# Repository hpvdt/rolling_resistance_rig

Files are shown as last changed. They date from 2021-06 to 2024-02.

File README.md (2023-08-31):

# Rolling Resistance Rig (RRR)

One of the most crucial aspects of our land vehicles is the study of rolling resistance and our pursuit of reducing it. To this end the team has constucted a rolling resistance rig (_RRR_) to characterize different wheels. This repository serves as **the definitive** collection of information related to the RRR and its tests: especially the sensor system design and data processing. 

The general principle of the RRR is that there is a large drum which acts as the riding surface for the wheel and is spun up to speed by an electric motor to simulate speeds of over 80 km/h. The wheel under test is installed above the wheel and is loaded to a similar level to the expected vehicle load prior to the drum getting spun up. Once the desired speed is achieved by the system, the power to the drum is cut and the drum/wheel combo is left to slow down by dissipating power primarily through their own rolling resistances.

During this slowdown the rotational period of each part is monitored and recorded over serial to then be analyzed and derive a rolling resistance for the wheel being tested. This processing is performed after the experiment is concluded in MATLAB.

The exact procedure for this process is outlined in a separate markdown file, [`test_procedure.md`](./test_procedure.md).

## Repository Organization

There are a few folders used to sort the different components of the system.

| Folder | Purpose |
| --- | ---|
| `analysis` | Primarily the MATLAB files used to process the data collected |
| `analysis/data` | Previously collected experiment data |
| `arduino` | Microcontroller code used to collect data. **USE THE `rolling_resistance` SKETCH!** |
| `doc` | Assorted documentation about the system design |
| `hardware` | Hardware files for custom circuit boards designed for this system |

## Software Used

A few programs are needed to fully operate the system. No additional configuration is needed to any of the software to run the system (e.g. installing custom libraries).

- **Arduino IDE** (**V 2.1.0** as of writting) for programming the microntrollers used (Arduino Nanos/Unos).
- **KiCad 7** for the most recent board's hardware files. The previous version was prepared in EAGLE.
- **MATLAB** for post-processing of the data collected.
- **Excel/LibreOffice Calc** to store some results.

## Future Improvements

- [ ] Record procedure to determine inertia characteristics of a wheel as part of this repository
- [ ] Improve the data processing scripts. *More information in its [readme](analysis/readme.md).*

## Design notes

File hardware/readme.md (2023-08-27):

# Rolling Resistance Rig Hardware

The hardware for the test is pretty simple since we have always used two 3-wire sensors to monitor the wheels' rotations. Even so, custom boards have been made to improve the robustness of the system from just a development board and jumpers while also acting as a training exercise for new members interested in electronics.

## Folder Breakdown

- `rolling_resistance` - **Most recent board design**, designed in **KiCad 7**. Designed to be manufactured as a proper *printed* circuit board.
- `previous` - Previous designs made in **EAGLE**. These were designed to be *milled* circuit boards.

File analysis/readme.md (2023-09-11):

# Rolling Resistance Analysis

These MATLAB scripts are responsible for converting the test results into rolling resistance characteristics for the wheels we've tested. 

The process is a partially automated but there is still some editing of the scripts needed for nice outputs. The basic operation process is:
1. Upload test results in a spreadsheet to the `data` folder (if adding new data)
    - `aero` for general rolling resistance runs. The naming scheme for files here is "<Wheel/Model> - <Contact/Separate> - <Left/Right> - <Pressure/PSI> psi", e.g. *"Grandprix - Contact - Left - 100 psi"*.
    - `inertia` used for inertia measurement calculations
    - `force` is data collected from trials to see the effect of loading on the results, keeping other factors constant.
2. Edit `script_config.csv` with a list of wheels and pressures to be analyzed together.
    - E.g. `Vittoria Corsa Open,100` for Vittoria Corsa Open tires at 100 psi
3. Edit `RRcalc.m` to have the right legend entries for the wheels
4. Run `RRcalc.m` to generate the characterization plots

## Future Improvements

- [x] Automatically derive the necessary legend entries for figures from user parameters
- [x] Derive permissible wheel names from data saved rather than a list in the script
- [x] Convert all data to CSV for easier reading by other systems, at least `aero`
- [x] Replace `xlsread()` instances with more modern functions
- [ ] Rework logic for multiple wheel, with potentially differing pressures

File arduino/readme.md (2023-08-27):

# Arduino Code

The data collection system is based around an Arduino Nano (previously an Arduino Uno) and is programmed using the Arduino IDE.

The most recent version of the system (`rolling_resistance`) uses digital sensors (magnetic/Hall effect) and interrupts to accurately measure rotational period and stream it to the host PC over serial. Previously analog sensors and polling was used which wasn't as temporaly accurate or reliable.

None of these sketches have any dependancies outside of the stock Arduino-provided libraries.

## Saving the Data

The Arduino will not save any of the data, it is simply responsible for streaming it to the host computer to be viewed over serial. To save the data one must either use some program to log incoming serial data, or copy the entire contents of the serial viewer window into a text file to make a comma separated file (`.csv`) or Excel workbook.

## Folder Breakdown

- `rolling_resistance` - Active system sketch. **USE THIS!**
- `old` - Collection of previous sketches used. Kept for archival purposes and if we change sensors.

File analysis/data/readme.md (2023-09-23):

# Summary of Directories

- `aero` for general rolling resistance runs, each wheel configuration needs four trials listed below. The naming scheme for files here is "<Wheel/Model> - <Contact/Separate> - <Left/Right> - <Pressure/PSI> psi", e.g. *"Grandprix - Contact - Left - 100 psi"*.
  - Contact coast down - drum spun right
  - Separated coast down - drum spun right
  - Contact coast down - drum spun left
  - Separated coast down - drum spun left
- `inertia` used for inertia measurement calculations 
- `force` is data collected from trials to see the effect of loading on the results, keeping other factors constant.

In this main data directory there is a file outlining the configurations used for some of the earliest collected data in `csv` format.

# Reading Test Data
In CSV files in any subfolder of data, there are five columns of test data collected by the Arduino:

These columns show: time (microseconds), rate (drum), # of revolutions (drum), rate (small wheel), # of revolutions (small wheel)

# Summary of Notable RR Results

*As taken from previous maintainer.*

- **Greenspeed** - 80 psi - Missing contact right, will you duplicate with contact left; **Note:** the data values from this test might be systematically off

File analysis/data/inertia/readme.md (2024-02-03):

# Inertia Test Procedure Outline

1. Add washers (m_coin) to wheel spoke and let wheel rotate like a pendulum.
2. Aim to record ~10 oscillations.
3. Upload data according to the procedure in 'analysis'

### Notes About the Data

Due to a previous configuration of the rotation sensors used for the rolling resistance rig, there were two recorded 'ticks' per wheel pendulum period, so alternating event entries were discarded. This has been done manually by altering the saved data to remove the ignored rows and removing the code to do the skipping so that the logic is *[hopefully]* easier to follow down the line.

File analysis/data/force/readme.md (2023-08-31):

# Force tests

Collection of data collected from some "force" test runs, no link to a specific wheel model. According to Calvin R. these were trials to see the effect varying our wheel loading would have on the results all else being kept the same (wheel and pressure mainly). 35 lbm corresponds to an unloaded rig, 215 lbm fully loaded.

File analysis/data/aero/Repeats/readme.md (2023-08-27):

# Repeat Trials

These are datasets for repeat trials of some wheels. They have been kept for possible use in the future.

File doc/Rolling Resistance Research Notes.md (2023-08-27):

# Rolling Resistance Research

# November 17, 2017

- Testing the Mich. Blue at 50psi
  - Finished the aero coastdown to the right and the full coastdown in both directions
- Testing Mich. Blue at 60psi
  - Finished aero coastdown and full coastdown

### Notes:
- The Michelin Blue tire has a tendency of resonating over 85 km/h. The amplitude is small, though the effect causes noticeable fluctuation (of around 0.5 km/h) in the data for wheel speed. It shouldn’t affect the data analysis significantly.
- Repeating the left aero coastdowns at 60psi- forgot to adjust the wheel circumference. For the right, the correction was applied as a ratio with the correct circumfrence

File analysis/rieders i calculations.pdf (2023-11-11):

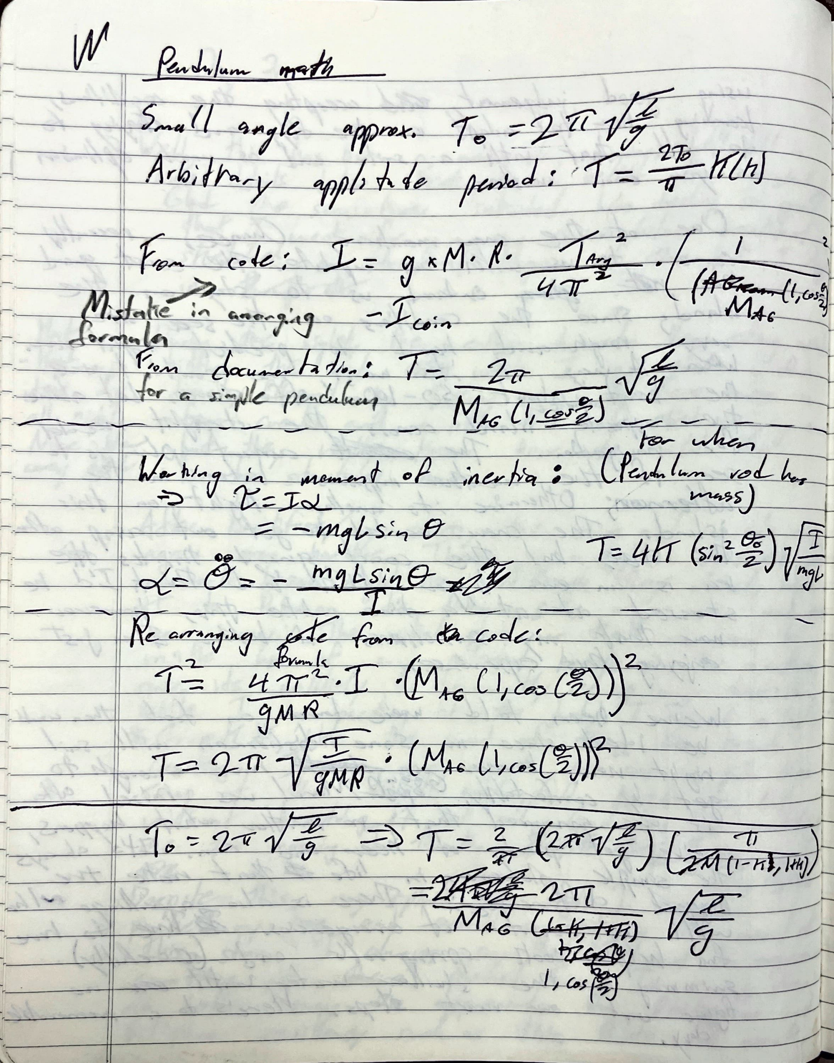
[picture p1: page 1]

| | .........__ ,
- - | -->+-.-.--.-----=-=- a~_ ,. | -

·--Jo-~~--=-~ uJ_,_. _ _.____ ' ----------r-'
=---++--_J___-=._--=~=----1- ·~~ - --'-----t+-------,--.f-lA--'-'-.1.__ ________ :__ ____ _ -_____:_____--+1----- | l | ,.- -----{--"---~ c~
-----++------,--t--=- | ' -r,; .. | . . | - r----:------
-:~-==:::t::~~~~==-~=-+5-~=--~~=-=-=-=-~~~~~=-=-=~~~=-~;__==~r G 1,-rt --v: 9 ~:s - ITYCRT ,-; ~ J= _ | f--:t-~(r-MJ;"i111f) ._ ---~-U--:----'------____:__ _____ :-Y:r-1..-~,r.,~t~-~ '2.--ry | -- | !._

I

-I
L

I

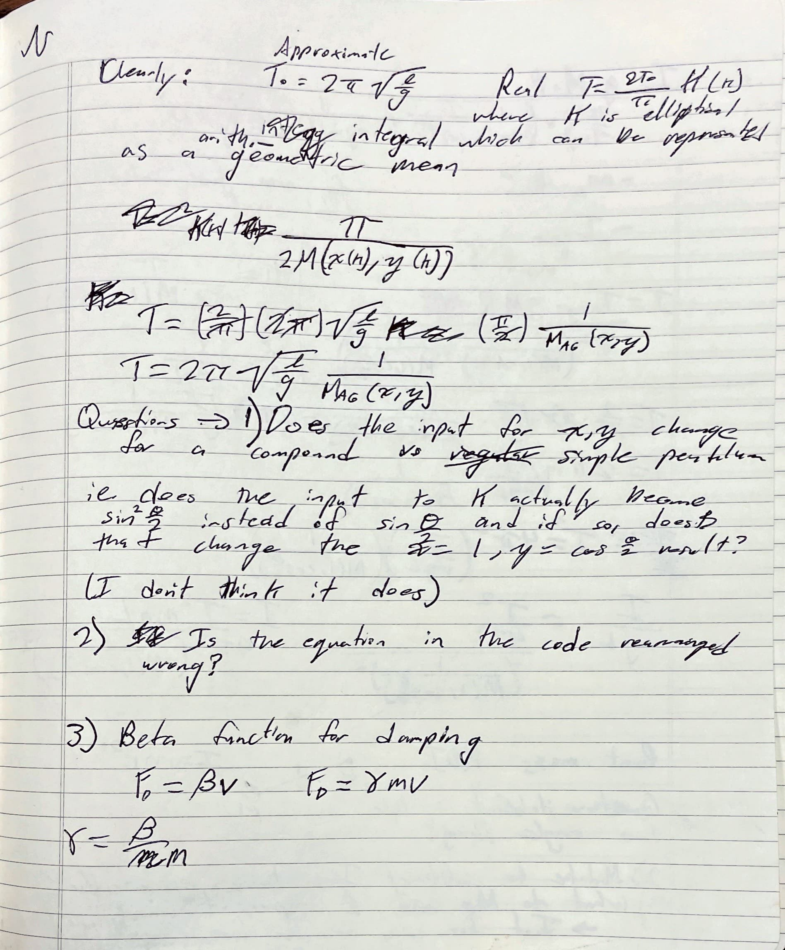
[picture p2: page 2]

------tt--'~~;L______±w-~-f-;.;., .,, :rt th-?_ uJe--~~c:/--,_

-------Jl-----== 'V'~v'8'v ?

·--

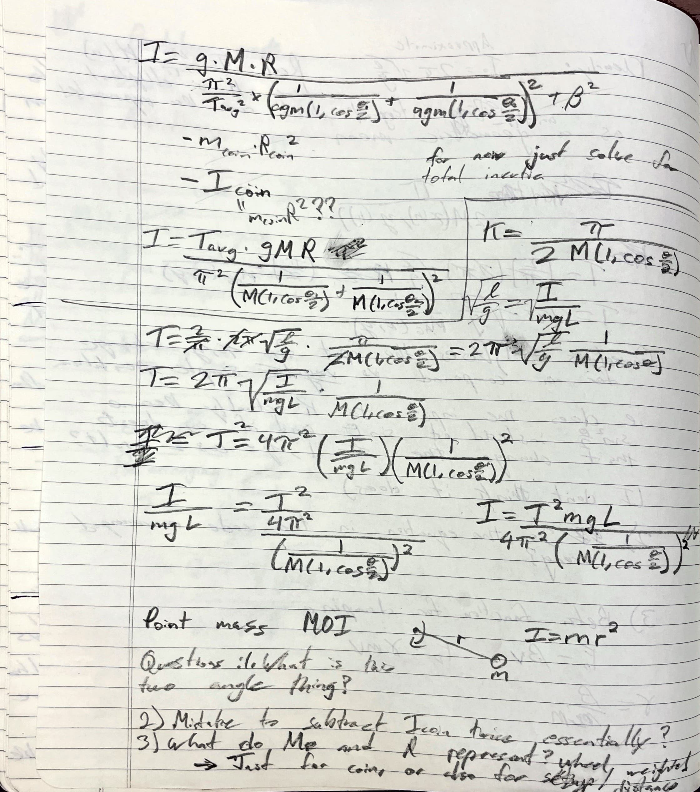
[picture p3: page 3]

---- | ---7)------. -7:'--= --z:...v. :~f--- ~ .;::. - ---~, - -_ -_ -_ -_ -_ -_-_ -_::J:::=:::::3~~--t,A- --,;-,...;:--- ------ -- | t1, c.$
=~--- -==::::::1~;:::;~~~~~~:_~~~~~~~~~;~~;;~-:s.=;~,;;~=---.

·----H-------~ ---------_ ⁻⁻

--~----p ~-- -- ~~------v----:.,,-------,J~=-r ---Z _ __ :::.rn~---1-r ___ _

I
" I,

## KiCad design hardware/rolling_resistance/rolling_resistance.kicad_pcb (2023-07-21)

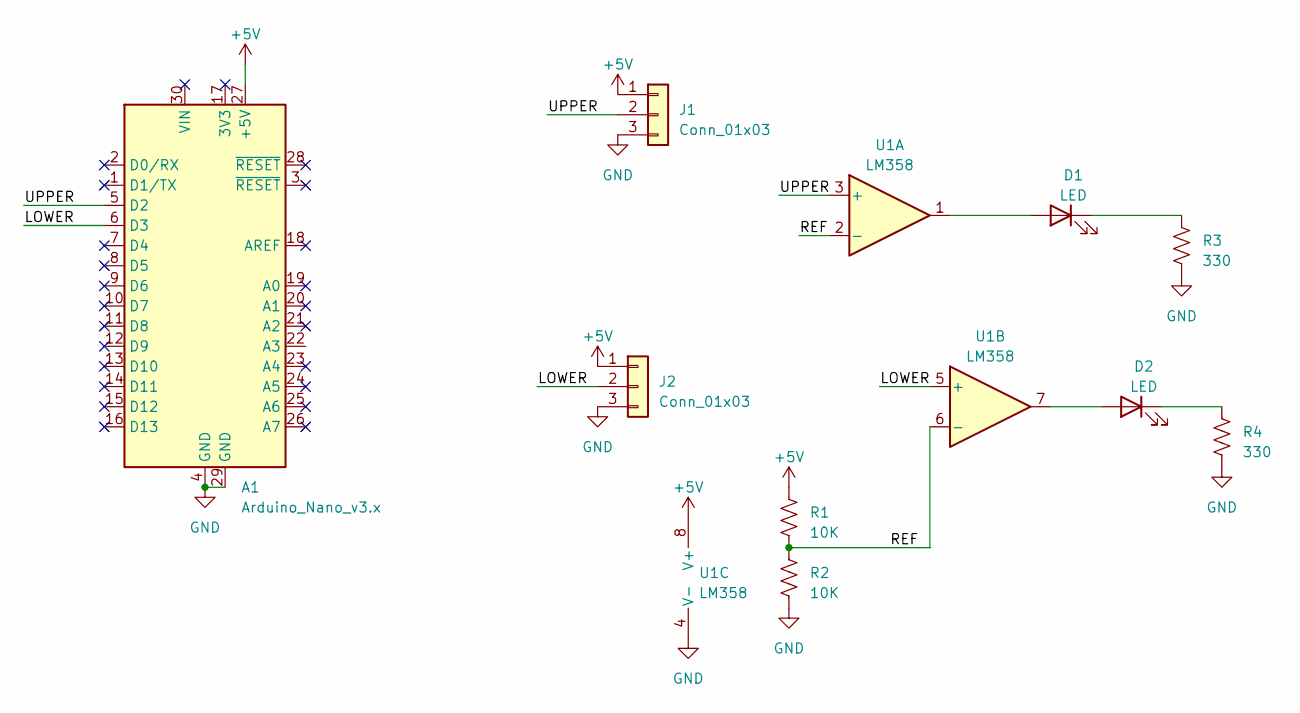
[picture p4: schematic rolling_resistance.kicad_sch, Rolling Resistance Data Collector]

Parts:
A1: Arduino_Nano_v3.x; Arduino_Nano
D1, D2: LED; LED_D4.0mm
J1, J2: Conn_01x03; JST_EH_B3B-EH-A_1x03_P2.50mm_Vertical
R1, R2: 10K; R_Axial_DIN0207_L6.3mm_D2.5mm_P10.16mm_Horizontal
R3, R4: 330; R_Axial_DIN0207_L6.3mm_D2.5mm_P10.16mm_Horizontal
U1: LM358; DIP-8_W7.62mm

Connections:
+5V: A1.27 (+5V), J1.1, J2.1, R1.1, U1.8 (V+)
/LOWER: A1.6 (D3), J2.2, U1.5 (+)
/REF: R1.2, R2.1, U1.2 (-), U1.6 (-)
/UPPER: A1.5 (D2), J1.2, U1.3 (+)
GND: A1.4 (GND), A1.29 (GND), J1.3, J2.3, R2.2, R3.2, R4.2, U1.4 (V-)
unnamed: D1.2 (A), U1.1
unnamed: D1.1 (K), R3.1
unnamed: D2.2 (A), U1.7
unnamed: D2.1 (K), R4.1

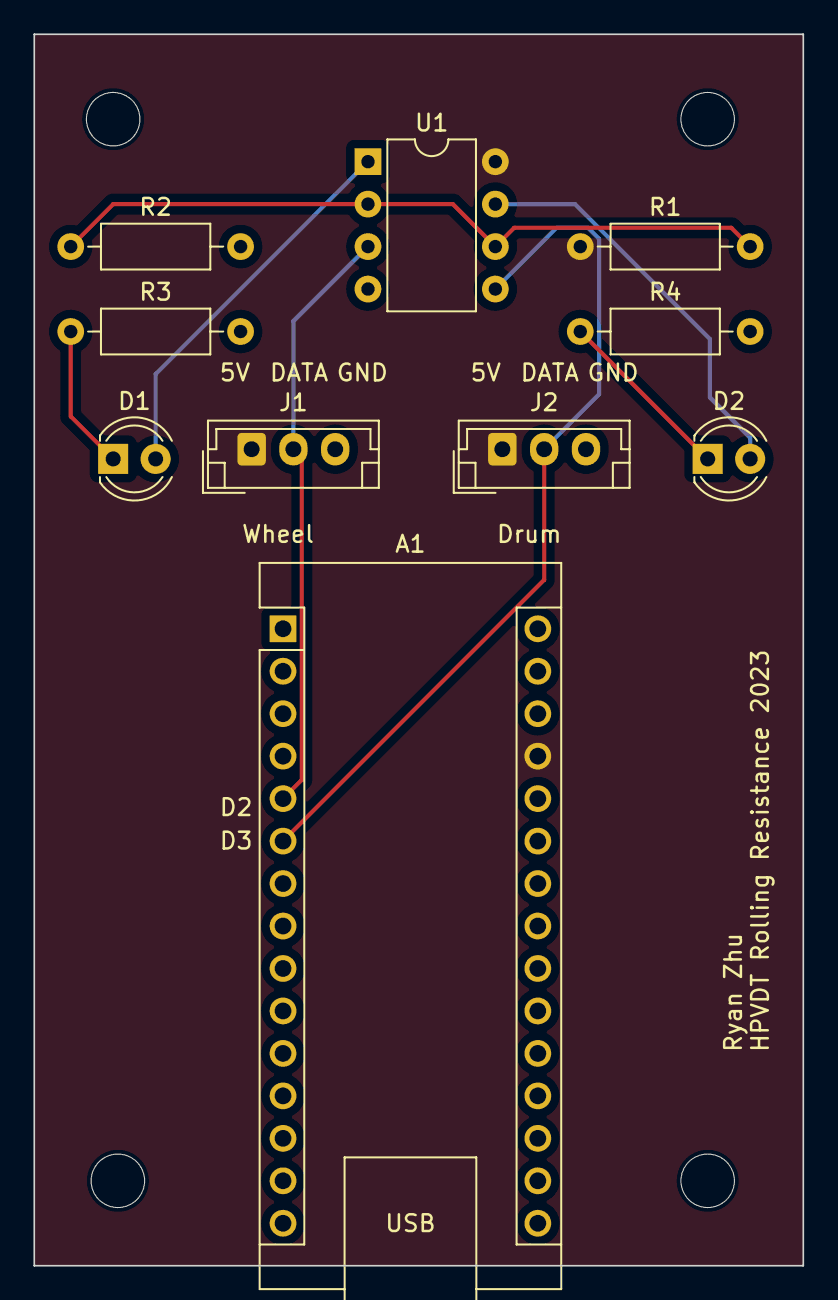
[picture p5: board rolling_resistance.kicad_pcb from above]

Board: 2 copper layers, 46.0 x 73.7 mm, 10 parts (0 on the bottom side), 9 nets.

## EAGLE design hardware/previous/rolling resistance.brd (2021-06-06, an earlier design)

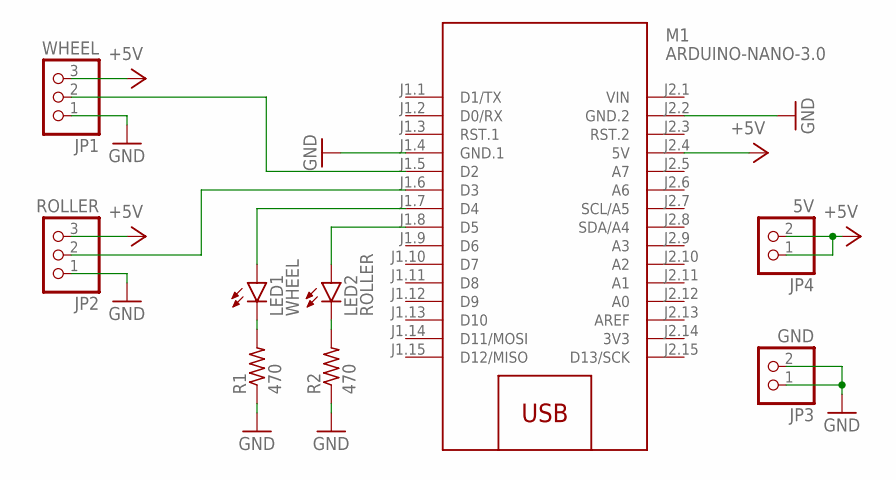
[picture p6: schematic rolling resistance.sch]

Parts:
JP1: WHEEL; 1X03
JP2: ROLLER; 1X03
JP3: GND; 1X02
JP4: 5V; 1X02
LED1: WHEEL; SML0805
LED2: ROLLER; SML0805
M1: ARDUINO-NANO-3.0
R1, R2: 470; R0805

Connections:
3V3: M1.J2.14 (3V3)
+5V: JP1.3, JP2.3, JP4.1, JP4.2, M1.J2.4 (5V)
GND: JP1.1, JP2.1, JP3.1, JP3.2, M1.J1.4 (GND.1), M1.J2.2 (GND.2), R1.1, R2.1
unnamed: LED1.C, R1.2
unnamed: LED2.C, R2.2
RLR_LED: LED2.A, M1.J1.8 (D5)
ROLLER: JP2.2, M1.J1.6 (D3)
VIN: M1.J2.1 (VIN)
WHEEL: JP1.2, M1.J1.5 (D2)
WHL_LED: LED1.A, M1.J1.7 (D4)

Board: 2 copper layers, 9 parts (0 on the bottom side), 8 nets, no tracks yet.

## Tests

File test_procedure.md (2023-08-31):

# Test Procedures

There are two tests that need to both be completed properly for us to be able to characterize the rolling resistance of a given wheel: the coast down test using the spinning drum, and another to determine the moment of inertia for a given wheel.

# Coast Down Test

This is the test most team members imagine the rolling resistance test to be given the imposing apparatus it depends on. In this test the wheel under test is mounted to our rolling resistance assembly and spun up to speed; generally reaching effective speeds of about 100 km/h using the motor powered drum and then power is cut and the coast down is measured. The process is bit more nuanced than that.

To isolate rolling resistance as the factor responsible for slow down from other factors, the wheels are coasted down twice: once in contact with the drum and the other time once the top speed is achieved the wheel is lifted and coasts down in air. Comparing these allows us to isolate the aerodynamic loss since it is the only factor affecting the "separated" coast down, and then we can subtract that effect from the slow down where the wheel is in contact to remove the aerodynamic losses, leaving just rolling resistance losses.

To improve the reliability of our results, these trials are performed twice with the drum is spun in opposing ways since there is a subtle difference in the results if the drum is spun one way or the other. We take the average of the opposing direction data sets to try and cancel out the effect of direction on the data.

Thus for each wheel configuration four data sets are prepared for these trials, these are all needed for post-processing.

1. Contact coast down - drum spun right
2. Separated coast down - drum spun right
3. Contact coast down - drum spun left
4. Separated coast down - drum spun left

# Inertia Test

In addition to the coasting data the moment of inertia for the wheels must be characterized before a rolling resistance can be derived.

*The exact procedure for this is currently being reviewed and will be posted here once settled.*

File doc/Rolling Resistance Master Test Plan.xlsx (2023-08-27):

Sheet: Testing Overview
Tire | Pressure (psi) | Load (lbm) |  | Separate Left | Separate Right | Contact left | Contact right | All done | Interia Test | Tire circ (m)
Michelin 4575r16 (black) | 30 | 125
Michelin 4575r16 (black) | 40 | 125 |  |  |  |  |  |  |  | 1.7
Michelin 4575r16 (black) | 50 | 125 |  |  |  |  |  |  |  | 1.487
Michelin 4575r16 (black) | 55 | 125
Michelin 4575r16 (black) | 60 | 125
Michelin 4575r16 (black) | 60 | 35
Michelin 4575r16 (black) | 60 | 215
Michelin 44-406 (blue) | 40 | 125
Michelin 44-406 (blue) | 50 | 125 |  |  |  |  |  |  |  | 1.15
Michelin 44-406 (blue) | 60 | 125 |  |  |  |  |  |  |  | 1.53
Michelin 44-406 (blue) | 70 | 125 |  |  |  |  |  |  |  | 1.537
Michelin 44-406 (blue) | 80 | 125
Greenspeed | 80 | 125 |  | ✓ | ✓ | ✓ | ✓ | ✓
Greenspeed | 60 | 125 |  | ✓ | ✓
Greenspeed | 70 | 125 | New Tube | ✓ | ✓ | ✓ | ✓ | ✓ |  | 1.519
Greenspeed | 90 | 125 |  | ✓ | ✓ | ✓ | ✓ | ✓ |  | 1.528
Greenspeed | 100 | 125 |  | ✓ | ✓ | ✓ | ✓ | ✓ |  | 1.532
Grand prix 4000 s2 | 100 | 125 |  | ✓ | ✓ | ✓ | ✓ | ✓
406 | 110 | 125 |  | ✓ | ✓ | ✓ | ✓ | ✓
 | 120 | 125 |  | ✓ | ✓ | ✓ | ✓ | ✓
 | 140 | 125 |  |  |  |  |  | ✓ |  | 1.994
 |  |  |  |  |  |  |  |  |  | 2.080
Vittoria Corsa Opens | 100 | 125 |  |  |  |  |  | ✓
Swabe 1 or pro 1

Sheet: Moment of Inertia Testing
Moment of Inertia Testing | Distance from center to weight | Average Period of Oscillation | Average Period of Oscillation (Drum)
Mich. Black |  |  | 9.78 sec
Greenspeed Scorcher | 21.3 cm | 3.82 sec

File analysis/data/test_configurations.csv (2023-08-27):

test name | wheel used | tire used | pressure (psi) | Force (N) | include in calculations | temperature (air) | temperature (tire) | tube | notes
test_19_2_2015_FMB20 | HED_FMB20B | Michelin 4575r16 | 50 | 59.7 | 1 | 18 | 0 | 0
test_26_2_2015_FMB20 | HED_FMB20B | FMB20B | 160 | 59.7 | 1 | 19 | 0 | 0
test_2_3_2015_FMB20 | HED_FMB20B | FMB20B | 160 | 59.7 | 1 | 18 | 0 | 0
test_4_3_2015_Custom4000_1 | VelocityA23_GP4000Custom | custom4000 | 140 | 59.7 | 1 | 18 | 0 | butyl
test_4_3_2015_Custom4000_2 | VelocityA23_GP4000Custom | custom4000 | 140 | 59.7 | 1 | 18 | 0 | butyl
Test_HED_FMB20_140psi | HED_FMB20B | FMB20B | 140 | 59.7 | 1 | 0 | 0 | 0
Test_HED_FMB20_120psi | HED_FMB20B | FMB20B | 120 | 59.7 | 1 | 0 | 0 | 0
Test_VelocityA32_GP4000Custom_120psi_Butyl | VelocityA23_GP4000Custom | custom4000 | 120 | 59.7 | 1 | 0 | 0 | butyl
Test_VelocityA32_GP4000Custom_100psi_Butyl | VelocityA23_GP4000Custom | custom4000 | 100 | 59.7 | 1 | 0 | 0 | butyl
test_12_3_2015_FMB25 | HED_FMB25 | FMB25 | 155 | 59.7 | 1 | 0 | 0 | 0
Test_HED_FMB25_160psi_1 | HED_FMB25Calvin | FMB25 | 160 | 59.7 | 1 | 0 | 0 | 0
Test_HED_FMB25_160psi_2 | HED_FMB25Calvin | FMB25 | 160 | 59.7 | 1 | 0 | 0 | 0
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

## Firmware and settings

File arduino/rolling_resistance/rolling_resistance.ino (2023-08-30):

/*
Rolling Resistance Rig

Sensor install for monitoring wheel rotational period is US5881 which is an open-drain Hall
sensor (drains when exposed to a magnetic field), so it needs a pull up. Sensor model for
the drum is not known exactly, but it is a latching sensor which outputs binary but needs to
be exposed to an alterating magnetic field with a pullup enabled (maybe pullup is not needed 
but this is untested).  
 */

// Circumferences for the wheels (in metres)
const float circTire = 2.0800; //old value 1.9622; //1.994 for grand prix
const float circDrum = 4.7900;

const unsigned long debouncingTime = 5000;  // Software debouncing to avoid counting noisy edges repeatedly (us after first edge until next can be counted)
const byte pinTire = 2;
const byte pinDrum = 3;
const char delimiter = ',';                // Delimited used for data printed. Originally a tab ('\t'), now a comma for easy creation of CSV files.
const int decimalDigits = 2;                // Number of decimal points of precision. Default is 2 if unspecified for a `print` function.

volatile unsigned int rotationsDrum = 0;
volatile unsigned int rotationsTire = 0;
volatile unsigned long messageTime = 0;     // Record when most recent event occured
volatile bool triggerMessage = false;       // Has an event occured to be printed
volatile float velDrum = 0.0;
volatile float velTire = 0.0;

void setup() {
  Serial.begin(115200);

  pinMode(pinTire, INPUT_PULLUP);
  pinMode(pinDrum, INPUT_PULLUP);

  attachInterrupt(digitalPinToInterrupt(pinDrum), drumInterrupt, RISING);
  attachInterrupt(digitalPinToInterrupt(pinTire), tireInterrupt, RISING);

  // Print in order to ensure that the right circumference is input to Arduino
  Serial.println(F("!!! BE SURE THAT YOU UPDATED 'circTire' IN ARDUINO CODE FOR TIRE UNDER TEST !!!"));
  Serial.print(F("Current value of 'circTire' (metres): "));
  Serial.println(circTire, 4);
  Serial.println();
}

void loop() {
  if (triggerMessage == true) {

    // Copy in data into temporary variables so interrupts during the printing stages don't change data mid-message
    // This is done in a short burst that cannot be intterupted
    noInterrupts();
    unsigned long tempTime = messageTime;
    float tempVelDrum = velDrum;
    unsigned int tempRotationsDrum = rotationsDrum;
    float tempVelTire = velTire;
    unsigned int tempRotationsTire = rotationsTire;
    triggerMessage = false; // Clear flag once data is copied
    interrupts();

    Serial.print(tempTime);
    Serial.print(delimiter);
    Serial.print(tempVelDrum, decimalDigits);
    Serial.print(delimiter);
    Serial.print(tempRotationsDrum);
    Serial.print(delimiter);
    Serial.print(tempVelTire, decimalDigits);
    Serial.print(delimiter);
    Serial.println(tempRotationsTire);
  }
}


void drumInterrupt() {
  static unsigned long prevTime = 0; // `static` so it carries between function calls without being globally scoped
  unsigned long currentTime = micros(); // Use micros since it is more accurate to real time than millis()
  // https://arduino.stackexchange.com/questions/692/arduino-time-keeping-using-millis-is-not-accurate-or-correct

  if (currentTime < (prevTime + debouncingTime)) return; // Return without recording if too soon after previous edge

  velDrum = circDrum * (3600000.0 / (currentTime - prevTime)); // Grouped calculations to keep operands of similar magnitude for each step
  rotationsDrum++;
  messageTime = currentTime;
  prevTime = currentTime;
  triggerMessage = true;
}

void tireInterrupt() {
  static unsigned long prevTime = 0;
  unsigned long currentTime = micros(); 

  if (currentTime < (prevTime + debouncingTime)) return;

  velTire = circTire * (3600000.0 / (currentTime - prevTime));
  rotationsTire++;
  messageTime = currentTime;
  prevTime = currentTime;
  triggerMessage = true;
}

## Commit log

2021-06-06 Initial proposed hardware
    [rolling resistance blank.brd, rolling resistance blank.sch, rolling resistance.brd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]
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2023-01-18 Initial commit of revised hardware
    [rolling_resistance.kicad_pcb, rolling_resistance.kicad_sch]
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2023-07-21 Updated hardware to what was ordered
    [rolling_resistance.kicad_pcb, rolling_resistance.kicad_sch]
2023-08-26 Renamed hardware folder to lowercase
    [rolling resistance blank.brd, rolling resistance blank.sch, rolling resistance.brd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]
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2023-08-26 Initial upload of analysis code as proved by Calvin R.
    [Drum_I1.xlsx, Grandprix - Contact - Left- 100psi .xlsx, Grandprix - Contact - Left- 110psi .xlsx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]
2023-08-26 Upload of previously collected data and documentation
    [60psi - 35lbm Right.xlsx, 60psi- 215lbm- Left.xlsx, 60psi- 215lbm- Right.xlsx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]
2023-08-27 Updated to digital interrupts
    Previous code was based on analog sensors and polling. Switching to digital sensors and interrupts simplifies the code and improves the accuracy of timing events.
    Also deleted the previous version to not be confused for the "actively" developed version.
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2023-08-27 Updated readme's
    [rolling resistance blank.brd, rolling resistance blank.sch, rolling resistance.brd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]
2023-08-27 Cleaned up documentation
    Removed redundant documents and combined similar documents (primarily into "Master Plan" doc).
    Converted test notes into Markdown for easier version control and glancing.
    [Master Test Plan.xlsx, RR Result Notes.xlsx, Rolling Resistance Master Test Plan.xlsx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]
2023-08-27 Updated processing to use CSVs for configuration
    Removed redundant Excel workbooks and added MATLAB .gitignore file
    [Test_info.csv, Test_info.xlsx]
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2023-08-27 Unified naming scheme for collected data
    Also cleaned up some redundant data in the folder
    [Grandprix - Contact - Left - 100psi.xlsx, Grandprix - Contact - Left - 110psi.xlsx, Grandprix - Contact - Left - 120psi.xlsx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]
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2023-08-27 COnverted `info_test.csv` to csv
    [info_tests.csv, info_tests.xlsx]
2023-08-27 Merged all inertia measurements into single folder
    [Drum_I1.csv, Drum_I1.xlsx, Drum_I4.csv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]
2023-08-27 Merged collected data into one directory
    Compared all both data sets deleting redundant copies and moving missing data to the MATLAB data folder.
    Also reduced the size of many Excel workbooks by deleting columns to the right of principle data.
    [60psi - 35lbm Right.xlsx, 60psi- 215lbm- Left.xlsx, 60psi- 215lbm- Right.xlsx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]
2023-08-27 Relabelled data folders
    Reflected changes in MATLAB scripts while breaking the `cd` commands into parts to be OS agnostic.
    Also minorly improved MATLAB function documentation.
    [60psi - 35lbm Right.xlsx, 60psi- 215lbm- Left.xlsx, 60psi- 215lbm- Right.xlsx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]
2023-08-27 Converted aero data to CSV format
    Will enable easier processing of data in other systems and save storage space
    [Grandprix - Contact - Left - 100psi.csv, Grandprix - Contact - Left - 100psi.xlsx, Grandprix - Contact - Left - 110psi.csv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]
2023-08-27 Returned Drum inertia file as Excel workbook
    [Drum_I1.xlsx]
2023-08-27 Renamed documentation folder
    [Rolling Resistance Master Test Plan.xlsx]
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2023-08-31 Clarification regarding the 'force' data
    Also converted the force data sets to .CSV.
    [60psi - 35lbm Right.csv, 60psi - 35lbm Right.xlsx, 60psi- 215lbm- Left.csv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]
2023-09-03 Uploaded Grandprix 406 measurements
    Tested 2nd September 2023 by Luke P. and Hannah D. Wheels described as "Continental Grand Prix 406 ERLKONIG 28 mm pressurized at 90 psi"
    [Grandprix 406 - Contact - Left - 90psi.csv, Grandprix 406 - Contact - Right - 90psi.csv, Grandprix 406 - Separate - Left - 90psi.csv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]
2023-09-06 Renamed Grandprix 406 wheels to reflect proper psi
    [Grandprix406 - Contact - Left - 120psi.csv, Grandprix406 - Contact - Right - 120psi.csv, Grandprix406 - Separate - Left - 120psi.csv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]
2023-09-10 Cleaned inertia data
    Converted all `.txt`s to `.csv` and deleted the redundant ones which had `.xlsx` files
    [Drum_I1.csv, Greenspeed Scorcher_I1.csv, HED_FMB20B_I1.csv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]
2023-09-11 Converted inertia data to `.csv` format
    Converted for better version control and reduced repository size. Also added a readme for the interia files.
    [Drum_I1.csv, Drum_I1.xlsx, Grandprix_I1.csv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]
2023-09-11 Simplified inertia recordings
    Previously all data had rows skipped due to how the sensors used to work on the rig, recording two event per rotation. Now the data and code assumes one event per rotation for easier interpretation of code and data preparation.
    [Drum_I1.csv, Drum_I4.csv, Grandprix_I1.csv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]
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2023-09-11 Renamed configuration file, moved test summary
    [script_config.csv, test_configurations.csv]
2023-09-11 Added space before 'psi' in data file names
    [Grandprix - Contact - Left - 100 psi.csv, Grandprix - Contact - Left - 110 psi.csv, Grandprix - Contact - Left - 120 psi.csv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]
2023-09-11 Converted all scorcher references to be consistent
    [Greenspeed Scorcher - Contact - Left - 100 psi.csv, Greenspeed Scorcher - Contact - Left - 70 psi.csv, Greenspeed Scorcher - Contact - Left - 80 psi.csv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]
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2023-09-11 Auto-legend, noted issues for multi-trials
    Current logic in `RRcalc.m` doesn't seem to properly account for multiple different wheels, with different pressure levels. **This MUST get addressed in the future!**
2023-09-14 Added completed pre-processed tests
    [Left Seperate.xlsx, Left Together.xlsx, Left, Separate.xlsx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]
2023-09-14 Add files via upload
    added 60 psi partially completed tests
    [Left, together, 60 PSI.xlsx]
2023-09-23 Converted Continental files to .csv
    [Continental - Contact - Left - 120 psi.csv, Continental - Contact - Left - 60 psi.csv, Continental - Contact - Left - 90 psi.csv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]
2023-10-28 Update Drum_I1.csv
    unscrewing up the excel file i screwed up
    [Drum_I1.csv]
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

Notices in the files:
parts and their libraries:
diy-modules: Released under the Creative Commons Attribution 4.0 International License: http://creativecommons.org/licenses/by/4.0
